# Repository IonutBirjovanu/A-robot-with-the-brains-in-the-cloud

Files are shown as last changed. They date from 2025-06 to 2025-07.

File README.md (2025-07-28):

# Cloud-Controlled Quadruped Robot with GPT Assistant

This project showcases the design and implementation of a 3D-printed quadruped robot powered by a cloud-based Large Language Model (LLM) to enable natural human-robot interaction. Combining embedded electronics, speech recognition, and AI decision-making, the system allows users to interact with the robot using voice commands and receive verbal and physical responses in real time.

---

## Overview

The robot is built around a modular architecture:

- **Raspberry Pi 5** handles high-level control and communication.
- **Arduino Pro Micro** controls the 12 servomotors via a PCA9685 board.
- **Sensors**:
  - Front-facing Pi Camera
  - Two ultrasonic distance sensors
  - Wireless USB microphone
- **Speaker** for voice replies (TTS using `espeak`)
- **Cloud AI Pipeline**:
  - Audio transcription: OpenAI Whisper API
  - Reasoning and dialogue: OpenAI GPT Assistants API
  - JSON response containing movement instructions and speech output

---

## Project Goals

- Combine a physical quadruped robot with a cloud-hosted LLM brain
- Enable speech-based interaction using voice commands
- Integrate real-time multimodal sensing and action
- Demonstrate interactive behavior through high-level LLM planning and low-level hardware execution

---

## Software Architecture

```mermaid
graph TD;
  A[User Voice Command] --> B[Pi Microphone];
  B --> C[Whisper API Transcription];
  C --> D[Prompt + Sensor Data];
  D --> E[GPT-4 Assistants API];
  E --> F[JSON Response];
  F --> G[TTS Output to Speaker];
  F --> H[Serial Command to Arduino];
  H --> I[Servo Movement Execution];
```

---

## Hardware Architecture

The robot is a 12-DOF quadruped platform built on a 3D-printed skeleton, using hobby-grade servos and embedded electronics, organized around a modular control architecture. The system separates high-level logic (handled by a Raspberry Pi) from low-level actuation (handled by an Arduino Pro Micro).

### Mechanical Design

- Based on the **SpotMicro** open-source design
- 3D-printed frame modified to fit:
  - Raspberry Pi 5
  - Battery pack
  - Custom speaker mount
  - Camera and ultrasonic sensors

Each leg has:
- **3 servos**: hip (horizontal), shoulder (vertical), elbow (vertical)
- **Total**: 12 servos, driven by a PCA9685 PWM driver

### Electronic Components

| Component | Role |
|---|---|
| Raspberry Pi 5 | Main computer (AI, sensors) |
| Arduino Pro Micro | Low-level servo control |
| PCA9685 Board | 16-channel PWM servo driver |
| TD-8125MG Servos (×12) | Joint actuation |
| HC-SR04 Sensors (×2) | Distance measurement |
| Pi Camera | Visual input |
| USB Microphone | Voice command capture |
| Custom Speaker | Audio output via `espeak` |
| Buck Converters | Power regulation for Pi & servos |
| 4S 18650 LiPo Battery  | Main power supply |

---

### Modular Hardware Design
```mermaid
graph TD;
    %% Power distribution
    A[4S 18650 LiPo Battery] -->|Power| B1[DC-DC Buck Converter<br>5V for Pi]
    A -->|Power| B2[DC-DC Buck Converter<br>6V for Servos]

    %% Power outputs
    B1 -->|5V Output| C[Raspberry Pi 5]
    B2 -->|6V Output| F[12x TD-8125MG Servos]

    %% Pi peripherals
    C -->|USB| D[USB Microphone]
    C -->|GPIO| H[2x HC-SR04 Distance Sensors]
    C -->|CSI| I[Pi Camera Module]
    C -->|USB| J[USB Audio DAC → Speaker]
    C -->|USB Serial| G[Arduino Pro Micro]

    %% Control path
    G -->|I2C| E[PCA9685 Servo Driver]
    E -->|PWM| F

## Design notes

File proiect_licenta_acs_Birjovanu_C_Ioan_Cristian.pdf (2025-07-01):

## UNIVERSITY POLITEHNICA OF BUCHAREST FACULTY OF AUTOMATIC CONTROL AND COMPUTERS COMPUTER SCIENCE AND ENGINEERING DEPARTMENT

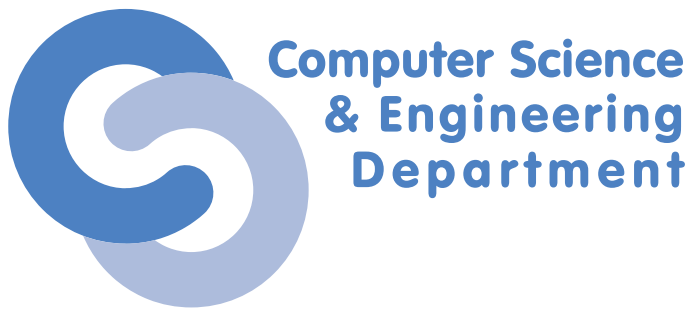
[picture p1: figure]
Computer Science & Engineering Department

# DIPLOMA PROJECT

## A Robot with the Brains in the Cloud Giving a LLM a quadruped robot body

# Bˆırjovanu Ioan-Cristian

### Thesis advisor:

### Conf. Iuliu Vasilescu

### BUCHAREST

2025

### CONTENTS

1 Introduction | 1
2 Background and Related Work | 5
3 Cloud-Integrated Control Software | 10
4 Quadruped Robot Design and Control (Hardware) | 28

5 Experimental results and Discussion | 38
6 Conclusions | 47
Appendix A System prompt | 51
Appendix B Sample Conversation with the Robot | 54

### ABSTRACT

This paper showcases the design and implementation of a quadruped robotic platform controlled by a Large Language Model (LLM) hosted in the cloud. The system aims to achieve a natural interaction between human and robot by offloading the high-level reasoning and decision-making tasks to a LLM, while the robot’s onboard components handles low-level movement control. The project’s architecture integrates a Raspberry Pi as the central piece, interfacing with an Arduino-based motion controller and sensors, including a camera, distance sensors, and a microphone.

A Python script collects the sensor data, including visual input and voice commands, and forwards it to the GPT Assistants API. The assistant processes this data and returns a response that includes movement instructions and a reply, enabling the robot to respond both verbally and physically in real time. The quadruped is based on a 3D-printed structure inspired by the Boston Dynamics Spot Robot, using 12 servomotors controlled via a PCA9685 module and an Arduino Pro Micro.

The paper highlights the two key components: a cloud-integrated AI control pipeline, and the robotic system’s design. Results show that the robot is able to understand spoken commands, respond accordingly, and demonstrate interactive behavior. This prototype provides a foundation for exploring LLM-powered physical agents and opens up possibilities for more advanced human-robot interactions in the future.

### 1 INTRODUCTION

Recent advances in Artificial Intelligence and hardware computing power are allowing robots to achieve higher reasoning and more advanced behaviors by using powerful models. For example, Boston Dynamics’ Spot robot [1] demonstrated the potential of autonomous quadruped robots in real-world scenarios.

Sadly, replicating those capabilities on a hobby-grade project is difficult due to the limited on-board computing capacity and complex software requirements. So, a popular workaround for lower computing capabilities and complexity is to offload the processing to the cloud, by using large language models (LLM’s) to handle high-level perception, reasoning, and decision-making.

This project aims to enhance a relatively low-cost 3D-Printed quadruped robot with a cloud-based intelligence, effectively giving the robot a ”brain in the cloud” that can understand spoken commands, speak with users and plan actions. By integrating a modern LLM (OpenAI’s GPT 4.1 [2]) as the robot’s reasoning system and using a simple onboard microcontroller for motor control, complex interactive behavior can achieved on lower-end hardware. The increased popularity of cloud AI combined physical robotics has the potential to greatly expand the accessibility to intelligent robots in research and education.

### 1.1 Motivation

This project started from an idea I got while watching a video on the OpenAI API [3] and how it could be used to control and navigate a robot around its environment [4]. The idea of creating a robot that would have the awareness of the average AI assistant was very intriguing at the time. After deciding upon using the OpenAI Assistants API for the so-called ”brains” part of this project, I started to look for ideas for the physical frame, the actual robot body. I was not sure what type of robot I wanted for this project, but I always thought about building a quadruped robot, similar to the Boston Dynamics’ Spot [1], and after searching for a ”3D-Printed robot dog”, I stumbled upon the SpotMicro project [5].

### 1.2 Aim and Objectives

The primary aim of this project is to design and implement a quadruped robotic system that combines a physical robot body with a cloud AI based on a Large Language Model(LLM). The robot should be capable of understanding natural language voice commands, responding verbally and with movement actions. To achieve this goal, I had to complete the following objectives:

- Developing a cloud-integrated software stack that can collect multimodal data (audio, video, distance), perform speech-to-text transcriptions, communicate with a GPT-based assistant in the cloud, and interpret the assistant’s replies, including movement instructions.
- Designing a prompt for the GPT assistant so that it produces useful and relevant

responses in a structured JSON format, that can be interpreted by the robot control system.
- Building a quadruped robotic platform inspired by Boston Dynamics’ Spot, using 3D Printing, servo motors for movement (3 per leg) and a microcontroller for the servo control.
- Implementing motion control firmware on the microcontroller that can parse the

high-level movement commands from the assistant and, move the leg servos accordingly (walking, turning, gestures).
- Integrating the sensors (camera, ultrasonic distance sensors, microphone) on the robot

and adding their data in the assistant’s message, enabling basic environmental awareness.
- Evaluating the system in example human-robot interaction scenarios, focusing on

the robot’s ability to execute voice commands, engage in simple dialogue, and move accordingly.

### 1.3 Contribution

This project brings several contributions related to the combined field of AI and robotics. Firstly, it demonstrates a practical architecture for a cloud-enhanced robot, where a local system uses a remote LLM for advanced natural language processing and decision-making. Unlike traditional robots, with all their processing taking place on-board, my project exemplifies the concept of cloud robotics [6], offloading computationally intensive AI tasks to remote servers.

Secondly, it contributes with a software pipeline written in Python[7] that combines Whisper speech-to-text transcription and GPT-4-based dialogue with control logic, illustrating how to integrate these advanced AI services into embedded systems.

Thirdly, this project showcases a custom hardware design for a 12-DOF quadruped robot (mechanically and electronically) and an Arduino control firmware that serves as a helpful robot agent that outputs natural language combined with action commands.

Finally, this work provides an analysis of the challenges (network delay, real-time control difficulties, sensor noise, and servo calibration) that I encountered while working on this project, along with documented solutions and recommended future improvements.

### 1.4 Results

The outcome of this project is a functional prototype of an interactive quadruped robot assistant. The robot can understand spoken user commands thanks to Whisper’s advanced speech recognition[8]. It can engage in a simple conversation with the user using GPT-4, which provides reliable responses to a wide range of questions. The GPT assistant is prompted to output a structured JSON in its replies, that include movement movement commands. Those commands are parsed and sent to the microcontroller, which in turn executes the corresponding servo movements. The robot can perform a set of movements, such as: walking forward, backward, turning left or right, standing, sitting, laying flat, waving and holding paw. Basic obstacle avoidance is demonstrated: if an object is detected by the distance sensors or observed in the camera view, the assistant will choose to not walk right into it, but to either avoid it using a turn command, or ask for a different instruction.

A sample interaction shows the robot engaging in a short dialogue, following a series of movement instructions given by the user, and responding accordingly when an invalid instruction was given (trying to avoid an obstacle that got too close). These results, detailed in the 5th chapter, validate the usefulness of integrating a cloud-based AI controller with a physical robot body. The system’s limitations were also observed - notably the approximately 5 second delay between speaking a command and the robot’s reply and action, due to network speed and API processing times.

### 1.5 Structure

The rest of this paper is organized as follows:

- Chapter 2 gives background information on cloud robotics, large language models, the

Whisper speech recognition model, and existing quadruped robot frameworks that inspired my design.
- Chapter 3 describes the implemented software architecture, including the sensor in-

terfaces, the voice transcription process, the integration with OpenAI’s GPT assistant (prompt design and JSON output parsing), and the logic for sending commands to the microcontroller.
- Chapter 4 details the robot’s hardware design and control: the mechanical construction of the quadruped (CAD and 3D printing), the servo control scheme using a PCA9685 driver, the electronics and wiring, and the Arduino program that interprets commands and generates coordinated leg movements. The physical challenges posed by the servo calibration and the gait stabilization are also mentioned.
- Chapter 5 presents experimental results and a discussion on the system’s performance.

We walk through an example user-robot conversation and analyze the response times, accuracy of the transcription and GPT responses, and the reliability of movement execution. It highlights the current limitations and the trade-offs made in this design (for example, the dependence on a reliable internet connection). In the last section, the future work directions are presented, such as improving autonomy with on-board processing, and expanding the robot’s list of skills.
- Chapter 6 brings and end to the paper, summarizing the achievements made with this

project.

The paper also includes Appendices with additional details: the full prompt given to the GPT assistant defining the robot’s control scheme and command format (Appendix A), and a sample conversation illustrating the robot’s behavior (Appendix B).

### 2 BACKGROUND AND RELATED WORK

### 2.1 Cloud Robotics and AI Assistants

The concept of cloud robotics refers to a robotics architecture where a big part of the computation and data storage are offloaded to cloud infrastructure, enabling robots to benefit from powerful remote resources via network connection. This contrasts with traditional robots that rely only on on-board processing. By using the cloud, even smaller robots can have access to advanced processing – for example, advanced AI models or shared knowledge bases – that would be impossible to run locally on limited hardware. Early versions of cloud robotics included networked robots sharing maps and skills (e.g. RoboEarth project[9]) and offloading heavy tasks like image processing to data centers.

In recent years, the expansion of IoT[10] and faster wireless communication has made cloud-connected robots more practical, and the model is seen in commercial products like Amazon’s Alexa devices[11] and Google’s Home assistants[12] (essentially stationary robots with voice interfaces that rely on cloud AI). This project builds on this idea: the quadruped robot uses the cloud for its AI assistant and voice transcription, which is a form of AI-as-a-Service[13] for robotics. One main advantage for this approach is that improvements or upgrades to the AI (e.g. a newer language model) can be used via an API call without changing the robot’s hardware. The trade-off is that the robot becomes dependent on network connection and suffers from higher latency in control loops, which must be addressed in the system design.

In particular, AI assistants[14] powered by Large Language Models have become accessible via APIs (e.g. OpenAI’s GPT-based services, including the new Assistants API[15]) that allow integration of conversational AI into applications. These assistants can follow complex instructions, retrieve information, and perform reasoning. By defining a suitable system prompt (role and instructions), we can customize the assistant’s reply in specific scenarios. In this project, I created a robotic cloud assistant – a custom GPT-4-based agent designed to interpret sensor data and user requests, then output both a conversational response and a robotic action. This approach is inspired by emerging frameworks like the OpenAI Function Calling capabilities[16], where the model can return structured data (like function arguments or a JSON) in addition to text. Rather than hard-coding robot behavior, we “prompt” the AI with the robot’s capabilities and let it decide the appropriate action, which is an example of using an LLM for high-level robot control. Prior works have started exploring LLMs in robotics: for example, Google’s SayCan[17] and related research combine LLMs with robot perception to plan actions from instructions, and community projects like MachinaScript[18] have demonstrated controlling Arduino-based robots via GPT-generated JSON instructions.

MachinaScript, in particular, outlines a pipeline where a central “brain” (a computer or a Pi) listens for input (voice or visual), uses an LLM to generate a sequence of actions in a structured format, parses these instructions, and then sends them to microcontroller “body” which executes them. My system uses a very similar pipeline, confirming that cloud-based brains for robots are a popular research direction.

### 2.2 Large language Models and GPT-4

Large Language Models like GPT-3.5 and GPT-4 are neural networks trained on massive text databases, capable of generating human-like text and performing a range of language tasks. GPT-4, introduced by OpenAI in 2023, is particularly notable for its ability to handle nuanced instructions and even accept image inputs. It exhibits what OpenAI describes as “human-level performance on various professional and academic benchmarks”, and is more reliable and creative compared to its predecessor. For the purpose of controlling a robot via natural language, GPT-4’s abilities fit well: it can understand context, reason about user requests, and produce intelligent multi-part answers. More importantly, GPT-4 can be guided via prompt engineering[19] to output structured data. We utilize this by instructing GPT-4 to format its responses in JSON with specific fields (like ”speech” and ”action”), effectively turning the free-form text generation into a fixed command interface for the robot.

One challenge with using GPT-4 (or any LLM for that matter) in robotics is ensuring correctness and safety of its outputs. LLMs are stochastic and can produce irrelevant or incorrect responses if not guided properly. They also have no built-in knowledge of a robot’s physical constraints. We fix this by carefully configuring the system prompt given to the model with explicit instructions and examples, explaining exactly which movement commands are available and what they mean. This aligns with how the author of the OpenCat framework[20] integrated ChatGPT with the Petoi Bittle robot dog[21]: by “training ChatGPT to understand what commands Bittle supports”, he made sure that the AI would respond within the robot’s abilities. The result, as reported, was a robot that could communicate and follow instructions with personality, dancing and performing tricks on command.

Similarly, this project’s GPT-4 assistant is made aware of the set of actions that the quadruped can do, and it’s instructed to avoid any output that doesn’t match the JSON format or tries something unsafe (like walking forward into an obstacle). GPT-4’s wide training data also means it can handle general conversations – if the user asks a question unrelated to movement (e.g. a trivia question), the model can answer factually while still remaining “in character” as a robotic dog.

### 2.3 Voice Recognition with Whisper

For the robot to receive commands in natural spoken language, a reliable Speech-To-Text (STT) engine is required. I selected OpenAI’s Whisper model for this task, thanks to its high accuracy and tolerance to noise and accents. Whisper is an open-source neural net trained on 680,000 hours of multilingual data, and it approaches human-level speech recognition performance. Unlike traditional keyword-based voice control, Whisper can transcribe free-form user speech, which is essential since the GPT assistant expects full sentence inputs (e.g. “Can you walk forward a few steps?” rather than a single pre-set command phrase like ”Ok Robot, move forward.”). There are two ways of using Whisper in this project: running it locally on the Raspberry Pi 5, or using a cloud API. Running the small Whisper models on a Pi 5 is doable, but it is quite slow (15-20 seconds for a 10-second long audio recording in my case), and uses a significant portion of the CPU, as noted in recent benchmarks of Whisper software on Pi hardware[22].

I instead opted for the OpenAI’s Whisper API for faster transcription, given that the robot is already internet-connected for the GPT assistant. The recorded audio from the robot’s microphone is sent to the Whisper API, and a text transcription is returned, usually in under 2-3 seconds for a short command. This cloud STT approach uses the cloud robotics philosophy and offloads the heavy lifting from the Pi. However, an offline fallback could be implemented in future versions for limited-case scenarios, making sure that the robot can still respond to basic commands in the absence of an internet connection (at the cost of slower and less accurate transcriptions). It’s worth noting that voice interface technology has a rich background in robotics and consumer devices. Systems like Amazon’s Alexa and Google’s Home Assistant introduced the scenario in which one can speak to a device and get intelligent responses. These systems also perform audio capture locally and send it to cloud servers for interpretation, so quite similar to what’s done in this project. The difference is that my robot does not just respond in words, it also acts with physical actions. This integration of voice commands, dialogue, and a physical body is a step towards more natural human-to-robot interaction. It was important to make sure that the transcription is accurate, especially for command phrases like “stop”, “forward”, “turn left”, since any misinterpretation there could lead to a wrong movement. Whisper’s accuracy on those simple words was great in testing, even with a bit of background noise and weird accents, thanks to its advanced speech recognition.

### 2.4 Quadruped Robot Platforms and Spot Micro

The mechanical design of my robot takes inspiration from existing open-source quadruped projects, particularly the Spot Micro family of hobby robots[23]. Spot Micro is a scaled-down, 3D-printed version of Boston Dynamics’ Spot, typically using 12 servos (3 per leg) forming the main joints: hip (horizontal translation), shoulder (vertical rotation), and knee (vertical translation). This provides a total of 12 degrees of freedom, which allows the robot to perform a wide range of leg motions and poses. Many makers have contributed with variants for Spot Micro. For example, the Nova Spot Micro project by Chris Locke[24] provides STL files and assembly guides for this robotic framework.

My robot uses a modified version of these community designs, adjusted to fit my specific components (The Raspberry Pi 5, a camera module, the speaker etc.). Low-cost quadrupeds like Spot Micro use hobby-grade servos for actuation. Common choices are metal-geared servos such as the TowerPro MG996R or DS3218, which provide decent torque (10-15 kgcm) at 6V and are affordable. However, as noted by hobbyists, a fully assembled Spot Micro can weigh a few kilograms, and using cheap or plastic-gear servos isn’t enough, as they will not be able to support the robot’s weight and can fail. In the beginning, I tried using TowerPro MG996R servos in my robot, but they proved to be difficult to work with (more details in Chapter 5). The servo calibration is an important process as well: each servo’s zero position must be aligned correctly when assembling the legs, and some trim adjustments have to be coded in, so that the robot stands evenly. The Nova Spot Micro project prioritizes calibrating the motors during leg assembly for proper movement. In my build, I used a servo tester (https://www.optimusdigital.ro/en/others/1162-tester-pentru-servomotoare.html) to get the correct angles while mounting the servo horns, making sure all the joints are symmetric.

Several electronic control architectures exist for DIY quadrupeds. One approach (used by Petoi’s commercial Bittle and Nybble robots) is to use a microcontroller (like an Arduino (https://www.arduino.cc/) or a Teensy) (https://www.pjrc.com/teensy/) for reading sensors and driving servos, and an optional Raspberry Pi (https://www.raspberrypi.com/) or ESP32 (https://www.espressif.com/en/products/socs/esp32) for higher-level tasks. Another approach is to use a microcontroller purely for motion control and a companion board (Pi or another MCU) for higher level logic and sensor data. My design uses the second approach: the Arduino Pro Micro (https://store.arduino.cc/products/arduino-micro) is used for servo control (“the body”), and the Raspberry Pi acts as the high-level processing unit for the sensor data and movement commands (“the brain”). This separation is useful because the servo pulses handled by the Arduino require precise timing, while the Pi, which runs a full Linux OS and resourceintensive software, can occasionally lag or spike in latency. This split architecture is also seen in OpenCat, (https://www.petoi.com/pages/opencat-open-source-robot-pet-framework) an open-source quadruped framework, which uses an Arduino-compatible board for locomotion and an optional Raspberry Pi for running AI algorithms.

Finally, we’ll look at the gait (https://www.animatornotebook.com/learn/quadrupeds-gaits) and control software in related work. Fully dynamic autonomous quadrupeds (like Boston Dynamics’ Spot) (https://bostondynamics.com/products/spot/) use advanced control algorithms, sensor arrays (IMUs, (https://en.wikipedia.org/wiki/Inertial_measurement_unit) vision, lidar (https://en.wikipedia.org/wiki/Lidar) etc.), and even machine learning to achieve advanced navigation. In the hobby space, simpler gaits (like crawling gaits where at least 3 legs touch the ground) or predefined walking sequences are typically implemented. Some projects use inverse kinematics (IK)[25] to compute leg joint angles for the desired foot positions, providing more flexibility in movements (e.g. the Alpha ESP32 Spot Micro[26] uses IK for motions like sitting and walking.

IK requires solving the servo angles for given desired XYZ positions of the feet relative to the body. I opted for not using IK in the leg positioning because of the issues encountered with the MG996R servos. (https://towerpro.com.tw/product/mg996r/) Instead, my robot’s walking gait is encoded as a series of key frames (servo angle sets) that move the legs in a cycle – an open-loop (https://focuskeeper.co/glossary/what-is-open-loop-system) approach. This method is enough for demonstrating walking on flat ground, though it lacks the adaptability of a full IK or feedback-controlled gait[27]. The implications of this choice (stability vs flexibility) are discussed in Chapter 4 and Chapter 5.

In summary, this project takes inspiration from prior work in cloud-connected AI, voice interfaces, and quadruped robotics. By combining these elements – a cloud AI assistant, a voice-controlled interface, and a quadruped platform, this project makes a solid entry in the interactive personal robotics space.

### 3 CLOUD-INTEGRATED CONTROL SOFTWARE

### 3.1 System Architecture Overview

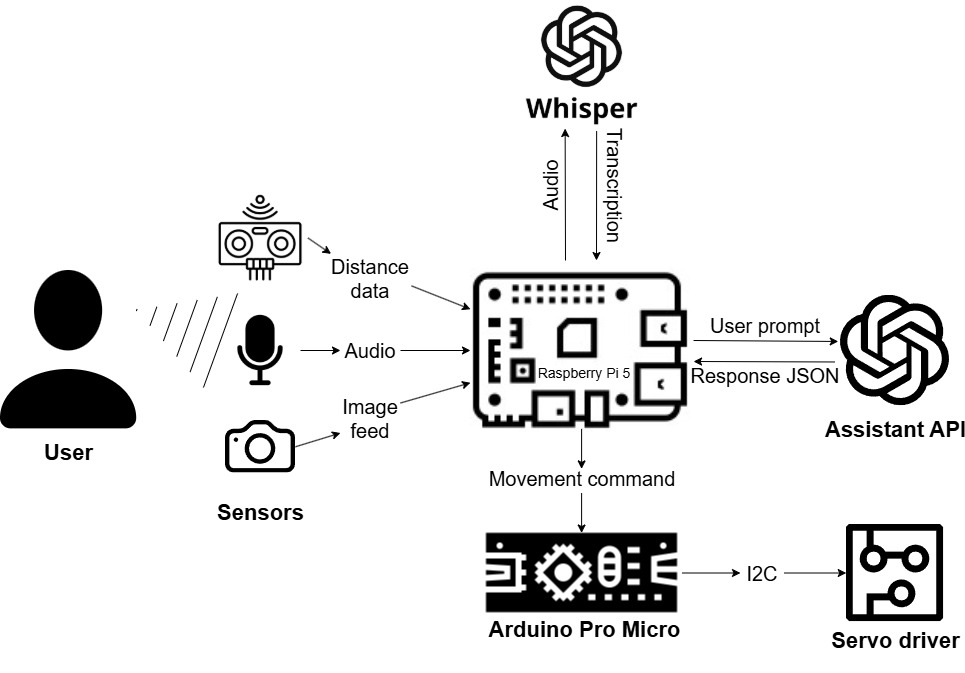
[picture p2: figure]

Figure 1: High-level system architecture, showing the flow from sensor input to robot motion.

The core of my system[28] is a pipeline that connects human input to robot action output via cloud API’s. Figure 3.1 illustrates the architecture. A user’s voice command is captured by the robot’s microphone, along with a picture from the Pi camera (https://www.raspberrypi.com/documentation/accessories/camera.html) and the data from the distance sensors, and then it is processed by the Raspberry Pi 5 (the onboard computer). The Pi runs a Python-based program that executes the following steps:

1. Input Reception: The raw audio is recorded at the beginning of the control loop for 10 seconds, then sent to the cloud-based Whisper API for transcription. The script also captures a picture from the front-facing camera and the distance readout from the 2 distance sensors, also mounted up front.
2. LLM Query Formation: The transcribed text from the user’s recording, along with the sensor readings (distance measurements and the camera feed), is formatted into a prompt, and sent to the GPT-4 assistant API. The assistant has been configured with a system prompt that gives it context about being a robot control system, the input data, its moveset, and the required response format.
3. Assistant Processing in the Cloud: The GPT-4.1 model, running on OpenAI’s servers - the “brains in the cloud” - receives the query and generates a response. Thanks to the given prompt, the response is a JSON object containing two main parts: a natural language reply to the user (the ”speech” field), and a set of movement commands (the ”action” field, which may contain a keyword like ”forward”, ”turn-left”, etc., or a direct control structure with parameters, and the ”steps” field - how many steps of the movement should the robot make).
4. Response Handling: The Raspberry Pi parses the JSON response. The ”speech” reply is extracted and is output via the speaker (running the Espeak text-to-speech (https://espeak.sourceforge.net/) software), and displayed (for debugging purposes, I logged it to the console). The action instructions are translated into a series of movement commands, which are sent over a serial connection to the Arduino board.
5. Microcontroller Servo Control: The Arduino receives the serial commands and executes the corresponding servo movements (e.g. starting a walking sequence or turning). This is the final step of the input-reasoning-action loop. After the Arduino reports back via Serial that the movement is finalized, the Python script will repeat all of the steps from above in the next loop.

With this architecture, the Raspberry Pi works as an intermediary between the cloud AI and the robot’s body. It handles all network communication and local sensor data. The Pi runs a Python script: it firstly configures all the components at the startup (the camera, Arduino Serial and the distance sensors) and announces via the TTS that the robot has successfully initialized, then it runs in a loop format: it asks for a command from the user, starts recording 10 seconds of audio, sends that recording to the Whisper API for transcribing, then, after the transcription is done, it packages it, alongside the camera picture and the distance sensors readout into a prompt, and sends it to the GPT assistant API for processing. I chose Python thanks to its vast library collection (for example, using the OpenAI Python library (https://github.com/openai/openai-python) to access the GPT assistant, and serial library for Arduino (https://pyserial.readthedocs.io/en/latest/pyserial.html) communication) and ease of use. In terms of performance, Python on the Pi 5 runs smoothly overall. Also, because the time constraints aren’t critical since the servo control is offloaded to the Arduino, I haven’t encountered any problems regarding the functionality of the robot. There are some delays introduced by the network, the AI processing times and the audio recording, but they don’t affect the functionality of the robot, and since the STT software is configured to run on a separate thread, the real-life experience doesn’t include significant delays.

The data flow and message formats are very important in this architecture. The recorded audio is handled in chunks of 10 seconds – the program loop starts a 10-second audio recording after a TTS message (in my case it’s ”Please give an instruction”). The audio is saved as a WAV file (https://en.wikipedia.org/wiki/WAV) and sent to the Whisper API. The returned transcription is inserted into the assistant prompt in the ”user instruction” field. Sensor data (the two ultrasonic distance readings in cm) is encoded as a small JSON snippet. For example, we have the ”environment data” field indicating 45 cm to an obstacle in the left and 50 cm to the right. This is due to the sensor angles being 50 degrees towards the center:

environment_data = (
"Left sensor: 45 cm (50° right-inclined), " "Right sensor: 50 cm (50° left-inclined)." )

These values are included in the user prompt to the assistant, alongside an image capture from the front camera. The GPT JSON reply will look like this:

{
"movement": "forward",
"steps": "4",
"speech": "Okay, I will walk forward."
}

Then, the Pi would process the output JSON. It will speak the ”speech” text using the TTS program and send the movement commands to the Arduino for the servo movement. In other interactions, the assistant might return something like this:

{
"movement": "left,forward,right",
"steps": "3,5,3",
"speech": "Obstacle detected. Walking around it."
}

Here, it observed from sensor data and camera feed that the forward path is blocked by an obstacle and decided to go around its left side. More details about the JSON structure in section 3.4.2.

One important addition is that I implemented basic error handling in the Pi’s software. If the Whisper API fails to return a valid transcription (network issue) or returns an empty one, it will fallback to a default case (”There are no instructions, act on your own”). If the GPT API call fails or returns invalid JSON, the Pi will log an error and retry in the next loop. To keep the processes in sync, only one GPT query is active at a time. Once the Arduino finishes executing a movement, it will send a “Finished Instruction” signal over serial, which the Pi listens for. This process helps to synchronize command execution (the Pi won’t send a new movement command until the old one is finished).

Overall, the system architecture represents a modular design: the cloud AI module, the Pi control module, and the microcontroller module work independently and connect through clear interfaces (API calls and serial commands). This modularity allows for future upgrades, such as using a fallback local LLM, adding additional sensors, or upgrading the hardware, all without rethinking the entire system.

### 3.2 Sensor Suite and Data Collection

The robot is equipped with a general set of sensors used for gathering the environmental context and the user instruction:

- Camera: A Raspberry Pi Camera Module (https://www.emag.ro/camera-ir-cut-compatibil-raspberry-pi-b-4b-ai478/pd/DY11J7MBM/?oid=240957149&scenario_ID=1) is mounted in the front of the robot and used

for capturing images of what is in front of the robot. In the current implementation, I didn’t add any on-board image recognition to run on the Pi, since I wanted to ”test” how much context would the AI be able to gather from the picture alone. Future versions could implement an object tracking feature and face recognition, so the robot could recognize users when looking at them and reply based on the person it’s talking to. The camera takes one picture for every loop, so every prompt sent to the assistant API includes visual data for context.
- Distance Sensors: Two HC-SR04 ultrasonic distance sensors (https://www.sparkfun.com/ultrasonic-distance-sensor-hc-sr04.html) are located in the front

of the robot, on one side and the other of the camera, each angled inward by 50 degrees. They are positioned like this purely because of the way the Spotmicro model (https://www.thingiverse.com/thing:3445283) is designed. The Raspberry Pi interfaces with these sensors through its GPIO pins (the trigger and echo pins for each sensor). The time (https://www.programiz.com/python-programming/time) Python library was used to handle the timing (emitting a 10 µs trigger pulse and measuring the echo pulse width for distance). These

values are then added to the prompt every time a query is made. The assistant can use this information to decide on movements. For example, if the right ultrasonic records a small value (less than 15 cm), the assistant will suggest avoiding the obstacle from the left (due to the inwards angle, these sensors help the robot determine the lateral obstacles, that aren’t covered by the camera FOV). Basically, the ultrasonic distance sensors give the robot a basic idea for obstacles, like the simple collision avoidance in a vacuum cleaner robot. (https://www.pcmag.com/picks/the-best-robot-vacuums) While GPT is not performing advanced path planning, it can output sentences like “I sense an obstacle in the right, I will turn left”, which proves a good environment awareness.
- Microphone A USB Wireless Microphone (https://www.alibaba.com/product-detail/Manufacturer-customized-round-2-4Ghz-mobile_1600363962435.html) is connected to the Pi for capturing audio

from the user. Since Whisper is optimized for noisy and unclear audio, the quality of the mic doesn’t have to be great. Although, these wireless mics are quite decent, and the rezulting transcriptions rarely differ from the real spoken phrase. The Python script uses the Arecord (https://linux.die.net/man/1/arecord) Linux library for recording audio. It opens a subprocess with the arecord command, selecting a 16kHz rate and mono audio channel, which is the recommended Whisper audio format. The audio is the only source of input from the user, and is automatically recorded in 10-second batches at the beginning of the script loop. A future improvement could include a separate program thread that continuously records audio, and when it detects voice activity (some noise after a period of silence), it sends that snippet to the Whisper API for transcription, avoiding the 10-second pause in the robot control loop for when the audio is recorded. Some specific voice commands could also be added, like the addition of a ”force-stop”, where the robot would suddenly stop when hearing the word ”stop” or ”pause” from the user.

### 3.3 Voice Command Transcription

The voice command segment converts the user’s speech into text that can be sent to the GPT assistant. As presented earlier, I chose the OpenAI Whisper transcription model (https://openai.com/index/whisper/) for this task. The whole transcription process works like this:

- At the beginning of the loop, after a spoken announcement via the TTS (”Please give an instruction”), the script starts recording a 10-second segment of audio, using the arecord Linux library. The recording segment of code is:

command = [
"arecord",
"-D", AUDIO_DEVICE,
"-f", AUDIO_FORMAT,
"-c", AUDIO_CHANNELS,
"-r", AUDIO_RATE,
"-d", str(RECORD_SECONDS), AUDIO_FILE
]

try:
subprocess.run(command, check=True)
print(f"[Audio] Recording complete. File saved as: {AUDIO_FILE}") except subprocess.CalledProcessError as e:
print(f"[Error] Recording failed: {e}")
- The recorded audio is then sent to either the Whisper API for transcription, or tran-

scribed locally using whisper.cpp. (https://github.com/ggml-org/whisper.cpp) The transcription method is decided by the boolean configuration variable USE API WHISPER (it has the value ”True” if we want to use the API, and ”False” for the local api). The audio transcription is sent to the Whisper API via this code:

transcript = ""
# Use the API to transcribe the audio print("[Whisper] Transcribing audio with API...")

try:
# Open the audio file

audio_file = open(wav_file, "rb")

except FileNotFoundError:
print(f"[Whisper] WAV file not found: {wav_file}")

try:
# Call the API to transcribe the audio

transcript = client.audio.transcriptions.create( model="whisper-1",
file=audio_file
)

except Exception as e:
print(f"[Whisper] Error during transcription: {e}")
- Next, we get the resulting JSON from the call, and extract the ’text’ field containing

the recognized speech. Whisper tends to include punctuation quite well, so I opted to send the direct transcription to the assistant API, to keep a small bit of context that would’ve been lost from text post-processing. One interesting observation though
- Whisper will transcribe everything it hears, so if the user says something and then there’s a prolonged silence or an ”umm...”, it will also include that. In the case where no speech was detected and Whisper returned an empty string, I added a feature so that the command will be changed to ”There are no new instructions, act on your own”.

The latency introduced by the transcription isn’t noticeable: recording 10 seconds of audio adds 10 seconds. Uploading that to the API and waiting for the transcription takes 2-3 seconds, which isn’t a long time. This is similar to a conversation with other popular voice assistants(Gemini, Siri, Alexa, where similar delays exist). Whisper can operate in different modes (translating to English, or just transcribing). I set it to translate to English since there are instances where the robot would be spoken to in my native language (Romanian).

Using Whisper yielded a high accuracy - in testing, even pretty complex phrases were correctly transcribed. Whisper’s tolerance to noise eliminates the need for a noise cancellation step. In one test, background music at an average volume did not affect the understanding of the command ”turn right” – it was transcribed correctly. This performance proves that using a modern AI-based automatic speech recognition (ASR) is a valid method for human input.

### 3.4 GPT Assistant Integration

This section describes the interface with the GPT-4.1 model via OpenAI’s API and how I configured the assistant’s output to match the robot’s architecture. The integration has two main components:

1. The Prompt Design, (https://www.promptingguide.ai/introduction/tips) which is responsible with the construction of messages (system and user prompts) sent to GPT-4 to receive the desired output.
2. The JSON Response Format and parsing, which describes how the Raspberry Pi extracts the assistant’s reply and the movement commands to be sent to the microcontroller.

### 3.4.1 Prompt Design

Designing the system prompt (also known as the initial instruction for the AI) is a very important step. My goal was to make the GPT-4 model act as a robot control system for a quadruped robot dog. The assistant has to include movement commands for every reply. I kept adding details for the system prompt as I developed each feature of the project and through experimentation. The final prompt (full text provided in Appendix A) can be summarized in these steps:

- Establishing identity:

You are a robotics control system for a quadruped robot. You receive:
1) The data from the robot’s distance sensors and an image of what he sees through its camera. The camera and the 2 distance sensors are frontally mounted. The camera is oriented straight ahead, and
the sensors are 5cm apart(on one side and the other of the camera), each rotated inwards by 50 degrees.
2) A user instruction - a voice command transcribed into text.

Give the robot a playful and curious personality, eager to discover the environment and people nearby.

- Establishing desired output format and clarifying the movement set:

You must output a JSON object with the following format:

{
"movement": "STRING", | // The actions that the robot will execute
- must be one of: forward, backward, left, right, stand, flat, sit, paw, greet . The actions are sepparated by commas
"steps": list of numbers, // Number of steps done for each movement,

only the forward,backward,left and right commands require a number of steps, for the others the number can be 0
"speech": "STRING" | // The text the robot should speak via TTS
}

Clarification and brief explanation of the poses:
- forward: the robot steps forward once, for around 4cm
- backward: the robot steps backward once, for around 4cm
- left: the robot spins left for one step, for around 10 degrees of rotation
- right: the robot spins right for one step, for around 10 degrees of rotation
- stand: the default position of the robot, standing straight
- flat: the robot lies down, touching the ground with its belly, similar to

its powered-down state
- sit: the robot sits like a dog, good for an idle position
- paw: the robot stretches one of its front feet in the front
- greet: the robot waves with an arm

This tells the model how to reply, making sure that the output can be parsed by the Pi.
- Valid output JSON examples:

Example of a valid json:
{
"movement": "forward,left,sit",
"steps": "2,5,0",
"speech": "Hello, I am moving forward, turning left, then sitting down" }

You can also only send one movement, like this:
{
"movement": "forward",
"steps": "5",
"speech": "Hello,I want to explore, moving forward" }

I listed some examples of valid output for the model.
- Guidelines:

Guidelines:
- Always return a valid JSON.
- If the space permits it but the instruction is unclear, try to turn the robot to the user and ask for clarification.
- If the users request is unclear, and the space is constrained so that you can’t turn, set the movement to a stationary position, steps = 0, and in speech, clarify what you need.
- As long as the space permits it, try and explore the environment you’re in, unless given a clear command from the user.
- Steps values should be integers.

These guidelines were added to increase the answer reliability and set the desired action responses.

I also added an experimental direct control schema to the prompt: instead of a default movement like ”forward”, or ”left”, the agent could send the angle position for every servo index. This was mostly implemented to test the reasoning capability of the GPT model for the direct positions. The prompt is:

There is also the option of a direct position control: You could have a json like this:
{
"movement": "1:30 2:80 5:100,2:60",
"steps": "2,0.5",
"speech": "Hello, I am moving the servos directly now"
}

In this way, you can directly set the angles for each servo on the robot. The movement consists of a list of servo indexes and their values. Different positions are sepparated by commas. The steps value now represents the amount of time each direct position is held.
The positions don’t reset after the timeout, the legs remain in those positions, but you can use the delays for orchestrating new movements. You can set a position, put a step value that determines the time it holds that, then add a new movement with a new time period to create your own complex movements.

The indexes of the servos are:
Each leg: [hip, shoulder, elbow]
{0, 1, 2}, | // Front left
{4, 5, 6}, | // Front Right
{8, 9, 10}, | // Rear Left
{12, 13, 14} // Rear Right

The indexes go from 0-15, but we’re not using the 3, 7, 11 and 15 indexes.

The positions for each servo that the robot uses in the standing pose are:
{40, 50, 65}, | // FL
{100, 90, 80}, | // FR
{45, 100, 80}, | // RL
{90, 60, 70} | // RR

And the positions for the laying flat pose are:
{0, 15, 65}, | // FL
{140, 130, 80}, | // FR
{0, 140, 80}, | // RL
{140, 10, 70} | // RR

The angles go from 0-180, but I recommend only going up to ~140-150, and be careful with the elbow 2, 6, 10, 14 servos - they have less movement space because of the robot’s joints, and can try to bend into the frame, so not reccomended to flex them a lot.

More info about the direct control schema can be found in Section 3.5.

All these instructions were combined into a single system message. This resulted in a long prompt (several hundred tokens), but GPT-4 does not have any problem with that context length. I configured it as the system prompt in the OpenAI’s Assistants Playground. (http://medium.com/@niall.mcnulty/how-to-create-an-assistant-in-the-openai-playground-a-beginners-guide-4f5c5c12213a) then the user message (which contains the transcribed command and sensor data as described).

While testing the assistant, GPT-4 performed great with this prompt. I didn’t encounter any scenarios where the LLM output didn’t match the desired JSON format, and the environmental awareness was almost surprinsing. Again, more details about the results can be seen in the fifth Chapter.

### 3.4.2 JSON Response Format

The formatting of the AI’s response is very important, since the script running on the Raspberry Pi needs to read the movement instructions automatically. I chose the JSON format because it’s easy to parse in Python (using the Python json library (https://docs.python.org/3/library/json.html) ). The content of the JSON is basic: a ”movement” string, a ”steps” list and a ”speech” string.

To ensure that the LLM always returns a JSON, I set the ”Response format” field as a ”json object” in the assistants Model configuration. Also, the design of the JSON output means the system can easily be extended or integrated with other modules. For example, if we wanted a GUI to display what the robot wants to do, it can parse the same JSON. Or, if the Arduino got replaced with another microcontroller, the integration remains the same if it receives the same action strings.

### 3.5 Movement Commands

After the Raspberry Pi extracts a movement command (”movement” string) from the assistant’s response, it will send it to the Arduino, which controls the servos. The communication between the Pi and Arduino is achieved via a USB serial connection (the Arduino Pro Micro appears as a /dev/ttyACM0 serial device for the Pi). I configured the serial link at 115200 baud. The command protocol used designed for serial communication is simple: Each command is sent as a line of text, terminated by a newline character (”\n”). The Arduino program reads lines from serial and parses them. There are 2 types of commands:

1. Movement Commands: Sending a direct moveset command, like ”forward” or ”sit”.

The Arduino moves the servos in predefined positions based on the selected movement. In case of walking commands (e.g. ”forward”, ”backward”, ”left”, ”right”), the ”steps” field represents the number of times that moveset is executed (e.g. for ”left,2”, the robot takes 2 steps to the left). For the rest of the moves that represent just a pose (e.g. ”stand”, ”sit”, ”greet” etc.) the prompt instructs the AI to send a ”steps”=”0” value.
2. Position Commands: Sending a string with direct servo target angles by order index, like ”0:15 1:30 2:90”. This type of command was mostly used for debugging, but with enough details in the prompt, the LLM was able to control the servos directly as well. But, since the aim was to let the AI handle high-level planning, and have the low-level control run on the Arduino, the first option is used by default, leaving the second one for isolated cases.

To send the commands, the serial port has to be initialised first, so I open the serial with 115200 baud rate at the beginning of the script, and keep it open, to avoid resetting the Arduino mid-run. I also set timeout=1 so that reading from serial doesn’t block the script for too long. The Arduino will send back completion messages, like ”Finished instruction” or debugging info like ”Standing still”. Those are printed by the Python script for logging. On the Arduino side, the serial parsing is done in a simple loop: it reads words from the lines until the newspace, then compares the keyword from the received command against known commands. The code looks like this:

void loop() {
// Accept commands via Serial Monitor for now if (Serial.available()) {
String line = Serial.readStringUntil(’\n’); line.trim();
if (line.length() == 0) return;

if (line.startsWith("move,")) {
int first = line.indexOf(’,’);
int second = line.indexOf(’,’, first + 1);
String dir | = line.substring(first + 1, second);
int steps | = line.substring(second + 1).toInt();

if (dir == "forward") moveForward(steps);
else if (dir == "backward") moveBackward(steps); else if (dir == "left") moveLeft(steps);
else if (dir == "right") moveRight(steps); else if (dir == "stand") standPosition();
else if (dir == "flat") layFlatPosition(); else if (dir == "sit") sitPosition();

else if (dir == "paw") pawPosition(); else if (dir == "greet") salutePosition(); else standPosition();

Serial.println("Finished instruction.");
}

An important part of sending the movement commands was avoiding their overlap. I had to make sure that the Pi doesn’t send commands faster than the Arduino can execute them. So, if the robot receives multiple commands from one LLM query, it will send them in order, and wait for the Arduino to reply via serial with the ”Finished instruction.” string, so that it knows to hold on to the new command until the current completes. To achieve this, I implemented a busy-waiting (https://en.wikipedia.org/wiki/Busy_waiting) sequence of code that continuously reads the serial output until it detects the finished instruction string. While testing, because interactions are sequential and the received commands have relatively low numbers (1-3), this configuration worked well. The program loop waits until the robot finishes moving (which is only a second or two per position command, but around 5 seconds for a step forward/backward or a directional left/right). After the movement finishes, it restarts the loop with the recording of instructions and sensor data collection.

In summary, the movement command mechanism is a lightweight protocol that sends the “movement action” from the Pi to the Arduino. In the case of movement commands (which are mostly used unless special cases), it is doing a level of abstraction for the details of the servo movements and gaits, so the high-level AI doesn’t have to calculate the kinematics for the movement. This kind of separation is recommended in robotics: the high-level planner (AI) gives abstract actions and the low-level controller takes care of the precise movement. This approach is also seen in MachinaScript (https://github.com/babycommando/machinascript-for-robots) for example, where they use serial commands like ”A:45,10;B:0,10;” to specify servo targets, so very similar to my direct position approach. Though, my movement command is even higher-level (just choosing a pre-set command). Both methods have their pros and cons.

### 3.6 Movement Gaits

After I finished assembling the legs, I discovered a step that I overlooked: I didn’t know how to make the robot walk. I could have started from a community Spot Micro project and use its locomotion code, but I chose to implement it myself, which in retrospect wasn’t a great idea. So, I first started out by configuring the servos to have the robot stand up straight, using these values:

// The offsets for each leg servo
uint8_t legOffsets[4][3] = { {40, 50, 65}, // FL

{100, 90, 80}, | // FR
{45, 100, 80}, | // RL
{90, 60, 70} | // RR
};

Then, I implemented a function that changed the leg angles relative to the standing position, so it would be easier to code movements for it:

// Set servo angles relative to per-leg offsets
void setLegRelativeAngles(uint8_t legIndex, int8_t hipDelta, int8_t shDelta, int8_t elDelta) {
setLegAngles(

legIndex,
constrain(legOffsets[legIndex][0] + hipDelta, 0, 180), constrain(legOffsets[legIndex][1] + shDelta, 0, 180), constrain(legOffsets[legIndex][2] + elDelta, 0, 180) );
}

And after experimenting with this relative angle change function, I ended up with this forward gait:

void stepForwardCycle() {
// Phase 1: Lift FL + RR
setLegRelativeAngles(0, -10, -10, -10); setLegRelativeAngles(3, 10, -10, -10); delay(100);

// Phase 2: Swing FL + RR forward setLegRelativeAngles(0, -10, 20, 0); setLegRelativeAngles(3, 10, 20, 0); delay(100);

// Phase 3: Place FL + RR down setLegRelativeAngles(0, 10, 20, 0); setLegRelativeAngles(3, -10, 20, 0); delay(100);

// Phase 4: Lift FR + RL
setLegRelativeAngles(1, 10, 10, 10); setLegRelativeAngles(2, -10, 10, 10); delay(100);

// Phase 5: Drag FL + RR backward setLegRelativeAngles(0, 0, 0, 0); setLegRelativeAngles(3, 0, 0, 0); delay(100);

// Phase 6: Swing FR + RL forward setLegRelativeAngles(1, 10, -20, 0); setLegRelativeAngles(2, -10, -20, 0); delay(100);

// Phase 7: Place FR + RL down setLegRelativeAngles(1, -10, -20, 0); setLegRelativeAngles(2, 10, -20, 0); delay(100);

// Phase 8: Lift FL + RR
setLegRelativeAngles(0, -10, -10, -10); setLegRelativeAngles(3, 10, -10, -10); delay(100);

// Phase 9: Drag FR + RL backward setLegRelativeAngles(1, 0, 0, 0); setLegRelativeAngles(2, 0, 0, 0); delay(100);

standPosition();
}

I implemented the simplest mode of stepping forward on a quadruped, by lifting 2 legs at once, in the opposite sides of the robot (the front left leg with the back right leg, ant the front right with the back left), moving them forward, placing them down and dragging them back.

For the backwards stepping, I implemented those same steps, but mirrored the angles so the legs move backwards.

The turning gaits proved more challenging to program, but I ended up using the same strategy, lifting 2 legs at once and moving the other 2 to achieve the desired motion:

void turnLeftCycle() {
// Phase 1: Lift FL + RR
setLegRelativeAngles(0, -10, -10, -10); // FL setLegRelativeAngles(3, 10, -10, -10); // RR delay(100);

// Phase 2: Swing FL back + RR forward
setLegRelativeAngles(0, -10, 20, 0); | // FL backward
setLegRelativeAngles(3, 10, -20, 0); | // RR forward
delay(100);

// Phase 3: Place FL + RR down
setLegRelativeAngles(0, 10, 20, 0); | // FL
setLegRelativeAngles(3, -10, -20, 0); | // RR
delay(100);

// Phase 4: Lift FR + RL
setLegRelativeAngles(1, 10, 10, 10); | // FR
setLegRelativeAngles(2, -10, 10, 10); | // RL
delay(100);

// Phase 5: Reset FL + RR to neutral (drag forward/backward) setLegRelativeAngles(0, 0, 0, 0); // FL setLegRelativeAngles(3, 0, 0, 0); // RR
delay(100);

// Phase 6: Swing FR back + RL forward
setLegRelativeAngles(1, 10, 20, 0); | // FR backward
setLegRelativeAngles(2, -10, -20, 0); | // RL forward
delay(100);

// Phase 7: Place FR + RL down
setLegRelativeAngles(1, -10, 20, 0); | // FR
setLegRelativeAngles(2, 10, -20, 0); | // RL
delay(100);

// Phase 8: Lift FL + RR again setLegRelativeAngles(0, -10, -10, -10); // FL setLegRelativeAngles(3, 10, -10, -10); // RR delay(100);

// Phase 9: Reset FR + RL to neutral setLegRelativeAngles(1, 0, 0, 0); // FR setLegRelativeAngles(2, 0, 0, 0); // RL delay(100);

standPosition();
}

Although complete, the movement code could greatly benefit from further development and testing to optimize and improve it. There is also the option of implementing inverse kinematics (https://en.wikipedia.org/wiki/Inverse_kinematics) to improve movement.

### 3.7 Software Challenges and Trade-offs

Designing the software pipeline raised a couple of challenges, and I had to make some trade-offs. They are listed below:

- Latency and Real-Time Interaction: As mentioned, the total time from speaking a

command to an action execution took a few seconds. This is mostly due to the cloud API calls (Whisper and GPT-4) and the set 10-second recording time, instead of an automatic speech detection. While GPT-4 is very advanced, its replies take a bit of time: typical API response time for a short prompt and short answer was 3-4 seconds in my tests (which is quite good for a modern LLM). Adding the 2-3 seconds for Whisper and some overhead, I often got 5-6 seconds of latency in total. This latency, while noticeable, since it’s not exactly instantaneous, it’s decent in a conversation context. The user experience is also helped by the filler phrases I added via the TTS (e.g. the phrase ”Processing instruction..”, which runs on a separate thread, so it doesn’t have to wait for the api calls). There is also the option of using a faster model, like the GPTo4-mini, which could respond faster (1-2 seconds), but in practice the bigger model also performed well.
- API Reliability: Relying on external APIs adds extra points of failure. There were instances of network issues where the API calls would return error messages (due to failing to connect to the servers). But since the program runs in a loop, it uses a simple retry logic: if Whisper API call fails, the current loop will have no new instruction, and the GPT will act on his own. And if the GPT call fails, there will be no new actions, and the loop will start again. Thankfully, in my use case, the frequency of commands is quite low, so I never got close to the official rate limits of OpenAI (which allow much more requests per minute for Whisper and chat). Another important trade-off is the token cost: (https://openai.com/api/pricing/) each Whisper and GPT-4 API call costs money (although a very small amount per call). Over heavy use it can add up, which is not ideal for a freely roaming robot. For this prototype project though, it was fine (I barely ended up using 60 cents, and the minimum payment of credit for api calls is 5 dollars - so it’s not a real issue for a hobby project). But in the case of a commercial product or widespread deployment, the api pricing becomes meaningful - so a fully offline solution would be preferable in that case. The local processing is also something to consider for future work.

- Continuous Listening vs Set Interval of Recording: I initially wanted the robot

to be continuously listening for a wake word, like “Hey Robot!”. Implementing a wake word detector (like the Porcupine (https://picovoice.ai/docs/quick-start/porcupine-python/) or pyttsx3 (https://pypi.org/project/pyttsx3/) libraries) on Pi is doable, but integrating that with Whisper proved more difficult (so that I didn’t end up constantly sending audio to Whisper, which would consume more resources). In the end, I went with a 10-second listening period announced via TTS at the beginning of the loop, so that the structure would remain more back-and-forward between the user and the robot (the robot listens for a command, processes it, executes it and starts again). The trade-off is between technical complexity and user experience. But for a more advanced process, there would be a need to integrate a local wake-word model to trigger the rest of the pipeline only when the user addresses the robot, and let it act independently in the meantime.
- Sensor Data in the GPT Prompt: Sending sensor data to GPT helped with obstacle

avoidance. But GPT-4 is not a dedicated path planning algorithm, so it might not always know what to do with the sensor values. For example, if there is an obstacle in the front of the robot, and the user says ”go forward”, ideally GPT should output a refusal or walkaround action. The prompt tells it to do so. In tests, it did respond as expected most of the times, but sometimes it might say: ”I’ll try to move forward carefully.” which is not ideal because it’s ignoring the obstacle in a way. This highlights that using a general AI for critical logic requires very explicit instructions. A fix to this problem could be to add a rule in the code (e.g. the Pi checks the distance and changes any forward command with a stationary one, adding a mention to the command change in the next prompt to the assistant). I didn’t end up implementing a safeguard, since the GPT prompt itself was enough, but it is a good implementation idea for future work.
- Memory and Context: I used the assistants API for the GPT calls, so it automatically

keeps all the conversation history per session, with no need of sending the last message as a reference. A ”session” is basically an assistant thread created at the beginning of the Pi control script, so the robot would recall everything that was told to him in that conversation. Each query to GPT only included the user prompt, since the system prompt is defined in the assistants workspace. Although, the robot can’t remember a previous conversation for when it was last used, since for every boot cycle, the assistant thread changes. This means that the robot doesn’t recall older conversations, just what was told to him in the current session. I could technically create an assistant thread manually and change the code so that only that one thread would be used for API calls, but that would mean that the token usage would increase, and the query time would take longer. Also, there is the extra cost for the calls, but that is not a big issue, since it would still be difficult to go over budget. The trade-off is the loss of conversation history (the robot can’t remember your name if you told it the last time you spoke with it), but I didn’t really find it a big problem, since the current conversation scope was more relevant. For future improvement, maintaining the context through all the conversations could make interactions smoother.

In conclusion, the software side is what makes the robot interactive. By using advanced AI models and focusing on the prompt engineering and protocol design, the resulting system successfully combines a cloud AI with a physical robot, despite some latency and simplicity of motion. The challenges encountered while designing the system made me aware of the importance of fail-safes when dealing with AI outputs, the need for programming the AI’s outputs for the robot, and the user experience details of interacting with a semi-autonomous robot. These conclusions will help improve the next versions of the system, as discussed in Chapter 5 and 6.

### 4 QUADRUPED ROBOT DESIGN AND CONTROL (HARDWARE)

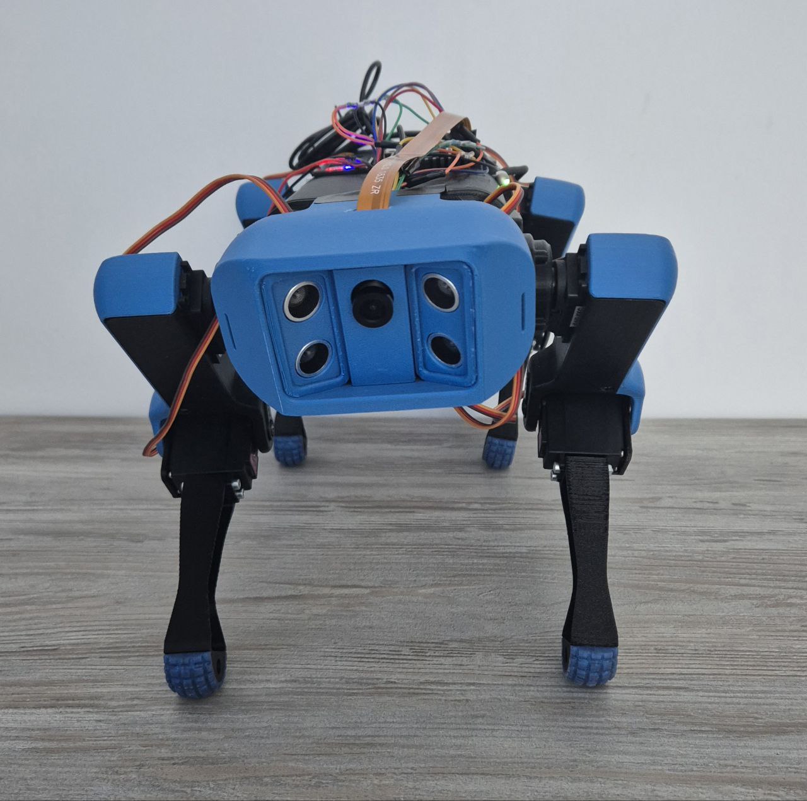
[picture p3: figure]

Figure 2: The finished robot, standing while waiting for a command

### 4.1 Mechanical Design and CAD Model:

The robot’s mechanical design is a quadruped structure, based on Boston Dynamics’ Spot (https://bostondynamics.com/products/spot/) and the open-source Spot Micro designs. (https://www.instructables.com/Nova-Spot-Micro-a-Spot-Mini-Clone/) Each leg has three segments (similar to the hip, thigh, and shin of an animal), that are moved by three servos, giving the robot 12 degrees of freedom in total. The design process involved two main tasks:

1. Obtaining the 3D models for the chassis and legs and modifying them for my specific usecase
2. Assembling the robot and calibrating the servos to provide the desired range of motion and stability

I started with existing CAD models from the internet. The frame of the robot is adapted from the project that started the SpotMicro community: KDY0523’s Spotmicro - robot dog, (https://www.thingiverse.com/thing:3445283) which provides the STL files (https://en.wikipedia.org/wiki/STL_(file_format)) for a miniaturized Spot clone that is designed to use 12 hobby-grade servos. (https://en.wikipedia.org/wiki/Servomotor) I imported these models into Autodesk Fusion 360 (https://www.autodesk.com/products/fusion-360/overview) to measure and modify them. The main modifications I made are:

1. Speaker Mount:

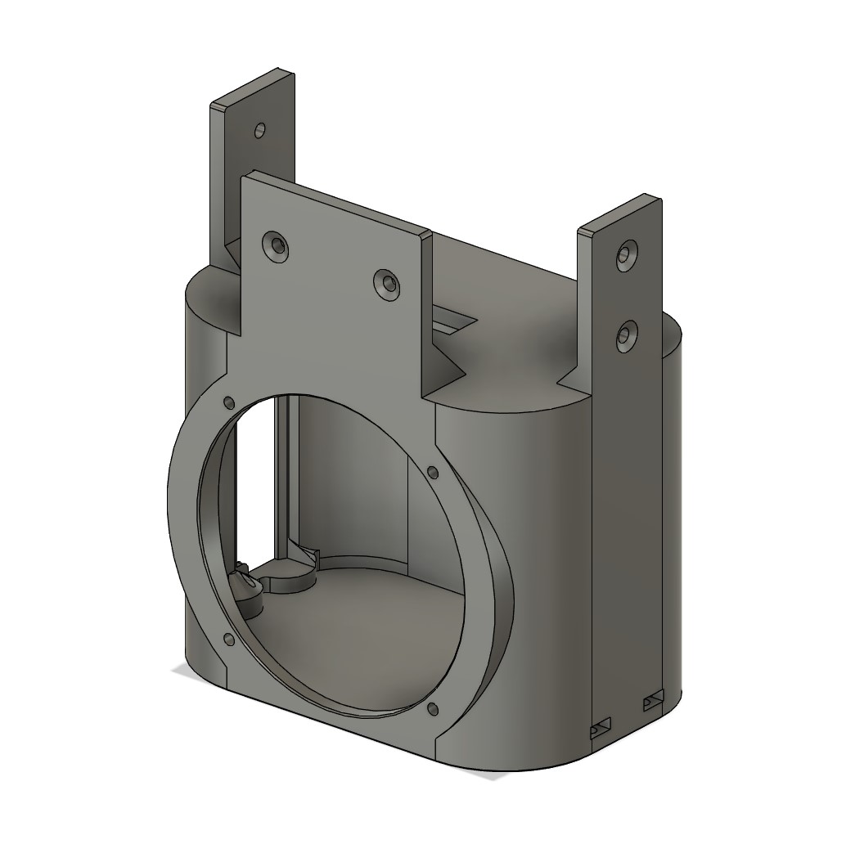
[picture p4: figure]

Figure 3: The designed 3D model for the speaker mount

For the robot to be able to respond to the user, it needed a speaker. I started from a Omega 5W portable speaker, (https://www.emag.ro/difuzor-portabil-fara-fir-pentru-dispozitive-mobile-omega-v4-2-tws-maro-deschis-og60w/pd/DC02PXMBM/) then disassembled it and saved the circuits. I sketched a rectangular box that would hold those parts and made it compatible with the robot’s front leg assemblies, so it could be mounted to them and act as the front half of the robot’s torso. To power the speaker, I used a MP2307DN buck converter, (https://www.emag.ro/set-10-x-convertor-descendente-ajustabil-retoo-bucking-step-down-mp2307dn-mini-360-cu-potentiometru-3a-4-5-23v-dc-dc-1-17v-e501/pd/DKG34VY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) and connected it to the Raspberry Pi via USB using an external audio card, (https://www.emag.ro/placa-de-sunet-usb-la-mini-jack-3-5-mm-adaptor-axroad-mall-plug-and-play-reducere-inteligenta-a-zgomotului-usor-de-folosit-pentru-casti-mi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) since the Raspberry Pi 5 doesn’t have a 3.5mm audio jack port.
This improvised speaker turned out to be effective, having the audio come straight from the robot. It did achieve quite a high volume, so there wouldn’t be any issues with users not hearing the robot.
To generate the robot’s response, as detailed in Chapter 3, I used the Espeak TTS library (https://espeak.sourceforge.net/) . I liked the retro and robotic sound of the voice, fitting for a robotic assistant.
2. Electronics Mount: This was a more difficult part to design. I needed something to connect to the speaker mount and the back legs, thus completing the robot body. I also needed to house the rest of the components that would make the robot work: the battery mount, the voltage regulator, the ampmeter, the Raspberry Pi, the Arduino Pro micro, and the PCA9685 module.
I placed the battery tray on the underside of the part, the voltage regulator on the side, leaving space for its heatsync and the Raspberry pi up top. The Arduino and the servo control module were seated in the remaining interior space, between the Pi and the battery.
After printing the mount, thankfully all parts fit in nicely and I was able to assemble the robot. The servo cables routed through the hole at the back and connected to the PCA9685 module, which was powered by the voltage regulator.

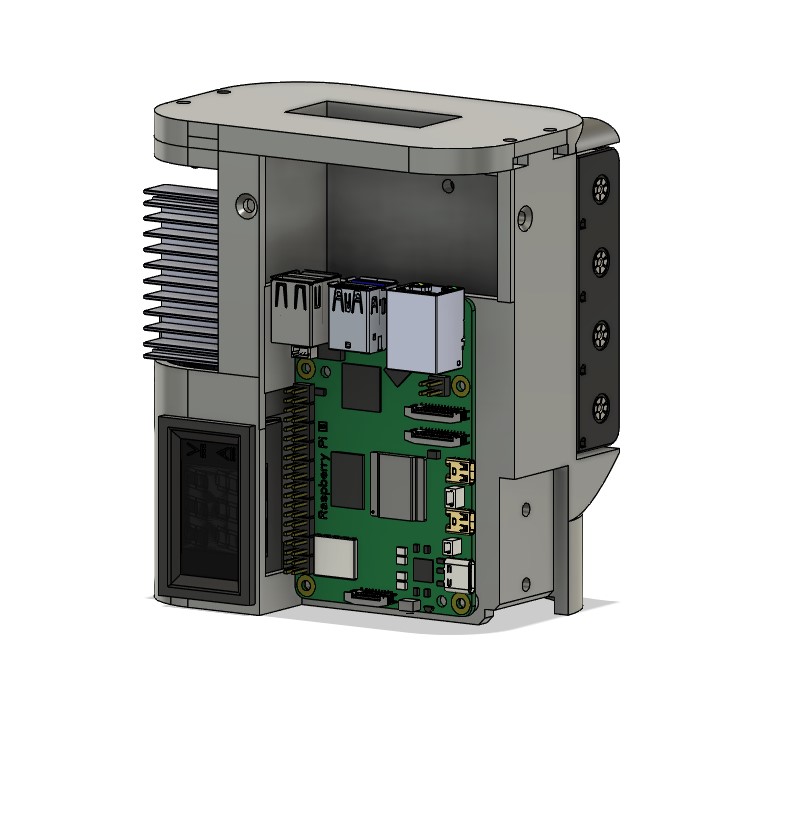
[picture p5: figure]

Figure 4: The designed 3D model for the electronics mount

3. Camera mount I wanted the camera to capture the front view of the robot. The front cover, which holds the ultrasonic distance sensors has an unused 25 mm wide space between the distance sensor mounts, the perfect space for the camera. I added 2 mounting holes to the underside of the cover, which I used to screw in the camera mount.
The model itself isn’t very complex, just a slanted profile to match the front cover angles, and a hole to pass the camera objective through.

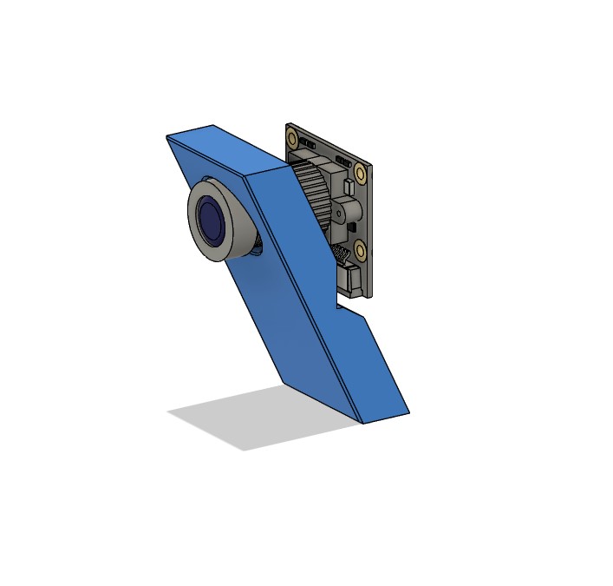
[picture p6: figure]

Figure 5: The designed 3D model for the camera mount

The parts were 3D-Printed[29] on my 2 machines: a Creality CR-10S Pro V2 (https://www.creality.com/products/cr-10s-pro-v2-3d-printer) and a Bambu Lab A1 Combo (https://eu.store.bambulab.com/products/a1?id=599117150694776844) using PLA (https://www.twi-global.com/technical-knowledge/faqs/what-is-pla) and PETG (https://all3dp.com/2/3d-printing-petg-comprehensive-guide/) filament at 15-20% infill with 0.4mm nozzles and 0.2 mm layer height. The structural parts (the black pieces of the legs and the torso) were printed from a combination of generic PLA (https://www.emag.ro/filament-pla-3dactive-1-75-mm-1100-g-negru-pla-1100-48043/pd/DYC4PB3BM/) and PETG, (https://www.emag.ro/filament-d-petg-easy-to-print-infix-1-75-mm-1-kg-220-260-c-negru-3/pd/DP942CYBM/) since I ran out of my PETG roll halfway through the printing process. The blue parts were printed in bambulab’s Matte blue PLA. (https://eu.store.bambulab.com/products/pla-matte?id=53926028673372) The total print time was around 40 hours for all the parts (torso parts, legs, brackets, mounts), but since I own 2 printers, I could print them in parallel, basically cutting the printing time by half. I encountered some typical 3D-printing issues, like holes not fitting screws perfectly and slight tolerance differences, but those were quickly solved with a drill and some sandpaper.

After printing the parts, I started assembling the components:

- Legs: Every leg assembly contains 3 segments: the tibia, which is the segment that

touches the ground and holds the knee servo, the hip, which is the middle segment, holding the hip flexing servo, and finally, the joint support for the last servo, the hip rotation actuator. Between the knee and hip servo there is an extra part, that supports the knee servo with a bearing.
- Front and back leg assemblies: Each leg assembly contains a left and right leg.

Those are held together by 2 supporting parts that act as a pelvis. (https://en.wikipedia.org/wiki/Pelvis)
- Torso: The robot’s torso is formed from the speaker and electronics mounts (detailed in Section 4.1). Those are the parts I designed to fit the custom electronics for this project. They use the existent mounting holes from the leg assemblies and interlock together using 6 M3 screws. When I was assembling the robot, I first had to install the electronics in their respective mounts (the speaker and electronics in the first part, and pretty much all of the electronics in the other), then slowly routed the leg servo cables from the leg assemblies through the parts, and into the servo control module.
- Front cover and camera mount: After completing the torso assembly, I moved to a

simpler one - the front cover assembly. Here, I first mounted the camera into its small support, then fastened it into the front cover, and added the distance sensors. I wired up the sensors and connected the camera ribbon cable, mounted the assembly in the front of the robot, and connected everything to the Raspberry.

One mechanical challenge was making sure that the robot could lift a leg without falling over, since the SpotMicro design is top-heavy, so the gait needs at least three legs on the ground at all times for stability. I did not implement dynamic balancing (e.g. by using a gyroscope), so the mechanical design has to ensure stability: I set the legs a bit wider by mounting the hip servos slightly to the exterior, and tuned their orientation further in the Arduino code. This small change helped with stability without affecting the walking process.

In conclusion, the mechanical design phase was a very important step in the making of this project. It required modifications and designing new parts from the ground up to accommodate my choice of hardware and ensure reliable operation. The result is a quadruped robot body that is capable of performing the movements ordered by the software while fitting all the electronics that give it full functionality.

### 4.2 Actuation: Servos and Kinematics

The movement of the robot is achieved with 12 servo motors arranged as described (3 per leg). These servos are standard RC (Radio Control) style servos that take a PWM (https://en.wikipedia.org/wiki/Pulse-width_modulation) signal to set an angle. I started with using the MG996R (https://towerpro.com.tw/product/mg996r/) (a popular low-cost metal gear servo), but they quickly proved to be sufficient for supporting the robot’s full weight. So, I ended up replacing most of the servos with the TD-8125MG (https://www.botnroll.com/en/servos/3655-metal-digital-servo-180-25kg-td-8125mg.html) model. Those really improved the motion of the robot. All servos run on 6V supplied from the battery via a 20A step-down regulator.

Servo characteristics: The MG996R and TD-8125MG servos both have approximately a 180 degree range, corresponding to a pulse width of 500-2500 µs, with 1500 µs as center (90 degrees). In practice, each servo’s actual range and center can vary slightly, and I calibrated them in the code by defining the servo offsets array (more details in Section 3.6). Their speed is about 0.2 seconds per 60 degrees at no load, but they’re slower under load. At first, when I started testing with the MG996R model, because of the robot’s weight, the knee servos in particular got overloaded when the robot was standing – they can hold the position but it draws significant current and they heat up if held for too long. Also, they can’t reach the standing position unassisted. Thankfully, using the TD-8125MG model mostly solved those problems.

PCA9685 servo driver: To control 12 servos, I ended up using the Adafruit 16-channel PWM driver board, (https://www.adafruit.com/product/815) based on the PCA9685 chip, which is connected to the Arduino via

I2C. (https://en.wikipedia.org/wiki/I%C2%B2C) This board generates 12-bit resolution PWM signals for all the servos without using the microcontroller’s timers, since the Arduino Pro Micro (Atmega32u4) (https://www.microchip.com/en-us/product/atmega32u4) has limited timers and could only directly control a few servos reliably. The PCA9685 acts as a hardware PWM controller: the Arduino sends it commands over I2C specifying channel and pulse width, and the chip handles the rest. As a result, the Arduino can send updates to servo positions and then continue with other logic while the PCA9685 continues outputting the required pulses. Another advantage is that it only uses two pins (SDA and SCL) to control all 12 servos, simplifying the wiring. I set the PCA9685 PWM frequency to 50 Hz, a typical value for servos (20 ms period). With 12-bit resolution, this gives pulse width increments of about 4 µs,

which is finer than the average hobby servo precision. I did not end up needing that fine of a resolution, but it is nice to have for future versions.

Kinematic configuration: Each leg’s kinematics can be described by two segments: thigh (upper segment) and shin (lower segment) and a base roll axis from the hip (to laterally move the leg). In the leg geometry, the thigh length is approximately 10.7 cm and the shin length is 13.4 cm (including the servo horn offsets). The default standing pose has both hip and knee at roughly 45 degree angles (0 degrees meaning the leg is fully extended straight down). In that pose, the foot is about 15-16 cm below the hip horizontally, giving the robot a standing height of around 16 cm, and a total height of approximately 23 cm including the body.

Gait Implementation: I decided to use a parallel gait for walking, where one leg moves at a time while the other three remain on the ground to support the robot. This gait is pretty stable if the center of mass stays in the triangle of support. The sequence is: lift front-left leg, move it forward, put it down, then rear-right leg, move it forward, put it down, and the same for the front-right and rear-left. After one cycle, the robot has moved forward. The turning gaits also only use one leg per movement to remain stable, but instead of advancing all the legs in the same direction, they reverse the directions for the diagonal legs to make the robot rotate (more details about the gaits and code in Section 3.6).

During testing, the TD-8125MG servos handled the load, but did get warm, especially the hip and knee servos after walking. This was expected, and thankfully they never overheated. The 3D models included supporting bearings on the knee joints and the lateral rotation of the hip, but none for the forward hip servo, where the whole leg was held only by the servo horn. In my case this didn’t affect the movement, but in future versions additional support for the hip would be recommended.

### 4.3 Electronic Architecture

This project, being this hardware intensive, needed a complex electronic architecture. The whole robot is powered by a 4-cell battery, situated in the back half of the torso. This battery then feeds the 3 voltage regulators, used for the servos, the Raspberry Pi and the speaker. The Arduino is powered directly from the Raspberry via a usb cable, and the Pi is connected to a 65W quick charge module (https://www.emag.ro/modul-incarcare-rapida-pd65w-cu-interfata-type-c-pd3-1-qc3-0-8-30v-dc-2-5mm-rx566/pd/DN7XBQYBM/) that is powered directly from the battery. The speaker is connected to the pi using an external audio card. (https://www.emag.ro/placa-de-sunet-usb-la-mini-jack-3-5-mm-adaptor-axroad-mall-plug-and-play-reducere-inteligenta-a-zgomotului-usor-de-folosit-pentru-casti-mi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)

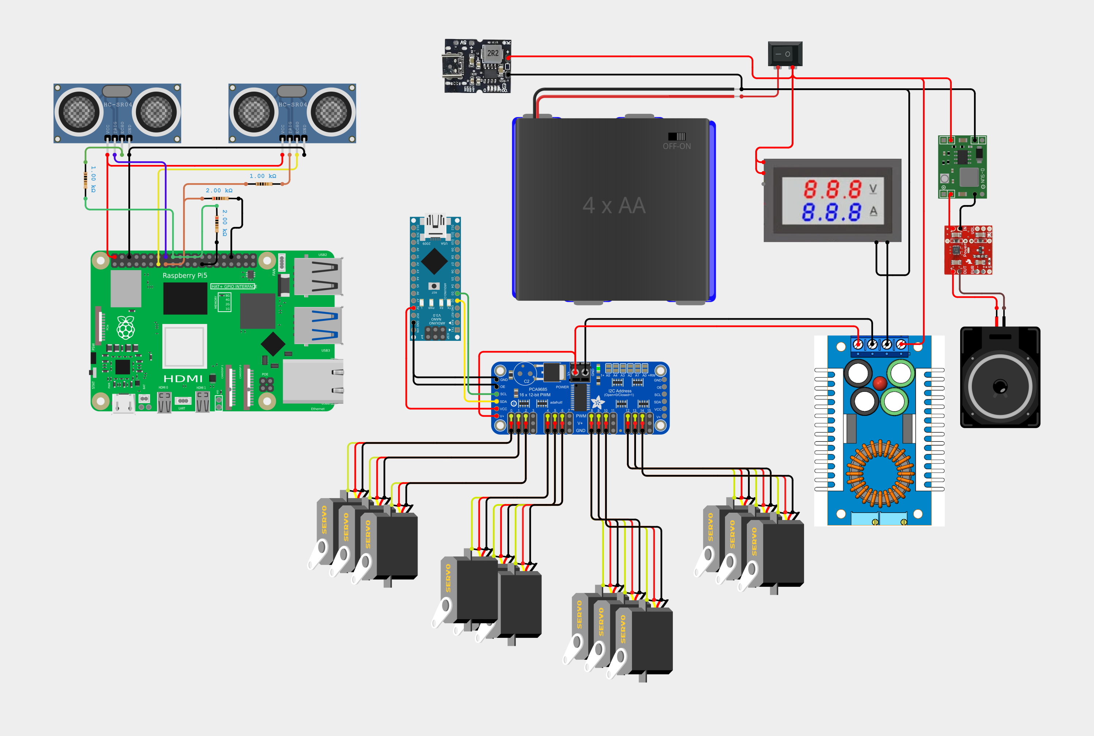
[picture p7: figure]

Figure 6: The wiring diagram for the project

Power Considerations: The robot is powered by a 4-cell 2200 mAh 18650 (https://en.wikipedia.org/wiki/18650_battery) battery pack. The individual cells are mounted in a 4x case. (https://ardushop.ro/en/cases-and-boxes/948-4x-18650-battery-holder-6427854012692.html) Running 12 servos simultaneously can draw a lot of current (a MG996R or TD-8125MG servo have stall power draws upwards of 2 A). To power them I used a 20A YD4020J (https://www.emag.ro/modul-sursa-de-coborare-tensiune-general-300w-20a-6-40vdc-gd-0032/pd/DYWYV8YBM/) regulator set to output 6V. It is wired directly into the PCA9685 board, using the power input terminal blocks. This feeds all the servos, greatly simplifying the wiring. The speaker and raspberry used separate voltage regulators as to not consume the servomotors’ power budget.

### 4.4 Arduino Firmware for Motion Control

The Arduino Pro Micro runs a program that interprets incoming serial commands and executes the corresponding motion sequences using the servos. It was written in Arduino C and structured to handle the different named actions. The main parts of the firmware are:

1. Serial command parsing (as described in Section 3.5): The Arduino is connected to the Pi via a USB cable, so it gets directly powered by the Raspberry, while using the same cable for Serial communication. The program runs a simple line parser in the loop to read the received commands.
2. Movement routines for each action: After the microcontroller receives a movement command and the number of steps for it, it executes the corresponding movement function for it, thus signaling to the servos to move in the desired direction. As explained in Section 4.2, I used a PCA9685 (https://www.adafruit.com/product/815) board to control the servos. It mostly helped on wiring, since it also supplied every servo with the connected power from the voltage regulator, so it reduced the need for power and signal cables to each servo. It was also simple to wire it up to the Arduino, since it used the I2C protocol, (https://en.wikipedia.org/wiki/I%C2%B2C) and only needed 6 pins connected.

In this project, the Arduino was only responsible for the movement of the servos, so it didn’t have any sensors connected. It worked well for this scope, but in future versions, adding a gyroscope (https://corporate.epson/en/technology/search-by-products/microdevice/gyro-sensor.html) or an accelerometer (https://en.wikipedia.org/wiki/Accelerometer) to help with uneven terrain and fall detection would be a good upgrade to the system, since any slope or uneven step could trip it. All the tests were conducted on a flat floor. I didn’t test outside or on rough terrain. The design can walk on carpets and wood flooring.

### 4.5 Sensor Integration and On-board Processing

Although the microcontroller didn’t have any sensors connected, this wasn’t the case for the Pi, as it had the following sensors attached:

1. The Distance Sensors: The robot has 2 Ultrasonic HC-SR04 (https://www.sparkfun.com/ultrasonic-distance-sensor-hc-sr04.html) distance sensors, which are used to gather more information about the potential obstacles in its proximity. They are mounted in the front of the robot, on one side and the other of the camera (which is positioned in the middle), and at a 50 degrees interior angle. This means that, for example, the right sensor detect the obstacles in the front-left side of the robot. The Pi runs a simple distance detection command on each sensor(by sending a 10 µs pulse and measuring the time it takes to return), and sends them to the assistant API, together with the user prompt and camera picture.
2. The Camera: The Pi camera is mounted in the front of the robot, where his ”head” is. It is held in by the camera mount part that I designed in Fusion (detailed in Section 4.1). It uses a ribbon cable (https://www.raspberrypi.com/products/camera-cable/) for the connection to the Pi’s camera port, and it is directly controlled by the Raspberry using the libcamera (https://github.com/raspberrypi/libcamera) library.
3. Microphone and Speaker: To record audio reliably, I used this wireless lavalier microphone (https://www.aliexpress.com/item/1005006802619837.html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) I got from Aliexpress for cheap. It proved to be a great choice, since the range is good (up to 10 meters) and the audio quality doesn’t affect Whisper’s transcription. The fact that it’s wireless also meant that the audio recording would work better, since a microphone mounted on the robot would add extra noise from the servo hum and have the user follow the robot and try to speak directly at it, instead of just holding the wireless microphone. And for the audio output (so that the robot can speak via TTS), I used a 5W portable speaker. (https://www.emag.ro/difuzor-portabil-fara-fir-pentru-dispozitive-mobile-omega-v4-2-tws-maro-deschis-og60w/pd/DC02PXMBM/) I removed its internals and transplanted them into the speaker mount (explained in Section 4.1).

In summary, the sensor integration was straightforward for voice and obstacle sensing. The ultrasonic sensors were used to inform the AI’s decisions, alongside the camera view, demonstrating how some simple sensors can make an AI-driven robot more grounded in reality, preventing ”mindless” instruction following.

### 4.6 Physical Control Challenges and Tuning

During building and testing of the robot, I encountered a couple issues that needed to be fixed:

1. Servo Calibration and Alignment: Although I set every servo to its middle position while mounting the legs using a servo tester, (https://ardushop.ro/ro/unelte/540-tester-servomotoare-6427854006301.html?gQT=1) so all the legs would sit in the standing position when the robot would get powered up, some of them (due to the manufacturing or the way I assembled the joints) moved to different positions. This issue was quickly fixed by introducing a servo offset array in the Arduino code to slightly adjust each actuator’s angle (code snippet in Section 3.6).
2. Thermal Issues: As expected, after a couple of minutes of use, the servos would start heating up, due to the load of keeping the robot standing. The temperature would slowly rise, but stabilise eventually. The servos got warm, but not burning hot, so about 50 degrees Celsius. It’s a good thing they stopped there, since the materials I used to 3D-print the legs (PLA and PETG) start softewning above 60 degrees Celsius. Thankfully, the servo temperatures didn’t pose a significant problem to this project, but for a future version it would be a great idea to add some heat syncs top the servos, or even some active cooling to keep them at lower temperatures.
3. Power issues: This was also a persistent issue for the project: The YD4020J, (https://www.emag.ro/modul-sursa-de-coborare-tensiune-general-300w-20a-6-40vdc-gd-0032/pd/DYWYV8YBM/) although rated for 20A, only put out around 15A max. This was fine for the most part, but in specific motions where all the legs would have to move at the same time (for example when the robot stand up straight after lying on the floor), the servos had a bigger power draw, which made the regulator voltage drop down 1-2 V . A reliable fix for this issue in future versions would be to use a more powerful regulator, or to add additional regulators to increase the power budget. I instead tuned the gaits and the motions to only ever use 2 feet at the same time, to reduce the load. This fixed the power draw issues, but it was more of a workaround than a fix.
4. Noise and Wear: Upon powering up the robot, the first thing that a user hears is the servo whine, caused by the actuator trying to hold its position. This is generally unavoidable, since any type of servo produces a buzzing sound when under load. More expensive models do emit less noise, but aren’t silent either. This doesn’t pose an issue for this project’s scope, but for a commercial version this might annoy some users. This could be fixed by upgraded actuators or a structural redesign. Another more significant issue could be the wear on the components. In my testing, and since the robot wasn’t built too long ago, I didn’t observe wear on any component except the old MG996R servos I used in the first version. But, after changing over to the TD-8125MG model, I didn’t notice any wear or degrading performance. This is due to the higher build quality and torque spec of the servos.

Overall, the physical tuning of the robot was an iterative process: I went back and forth between adjusting the servos and joints, to adjusting the control code. I even adjusted the AI prompt a couple of times to change the robot’s capabilities and range of movements.

The physical part of this project taught me a lot about servomotors, power delivery circuitry, battery configurations, and most importantly, the inner workings of walking robots.

### 5 EXPERIMENTAL RESULTS AND DISCUSSION

### 5.1 Example Interaction Scenario

To evaluate the integrated system, I conducted a series of test interactions that simulate how a user might interact with the robot. A representative scenario is the following (a full conversation can be found in Appendix B):

I start by saying, ”Hello robot!” to the robot. The robot’s microphone records this, Whisper transcribes it as ”Hello robot!”, and the text is sent to GPT-4 along with the sensor data (e.g. the ultrasonic sensors detect distances over 50 cm, so no immediate obstacle) and the camera feed. The GPT assistant processes the image, sensor data and camera picture, recognizes a human (me) in the picture, and responds in a friendly manner with the greeting motion. It returns this JSON:

{
"movement": "greet",
"steps": "0",
"speech": "Hello, there! How can I help?" }

The Raspberry Pi parses this and sends the speech to the TTS system and the commands over to the Arduino. The robot’s speaker outputs the voice audio, while the servos start moving in the predefined position. This greeting move is coded to have the robot sit on his hind legs, lift its left arm and wave it a few times, returning to the sitting position afterwards.

Next, I ask the robot to walk forward - ”Can you walk forward, please?” The transcription still picks this up, despite the background noise recorded by the microphone from the servos, giving us ”Can you walk forward, please?”. The assistant receives this, plus sensor data (there is enough space for the robot to move) and a picture of the room he is in, with plenty of space to explore, and me staying in the center. The assistant understands it as an instruction to start walking. It responds with:

{
"movement": "forward",
"steps": "3",
"speech": "Sure, I will walk forward." }

The Pi speaks ”Sure, I will walk forward.” through the speaker and sends the ”forward” command to Arduino. The Arduino executes the walking gait sequence 3 times. The robot rises from its sitting position and moves forward a for 6 steps (a movement gait does 2 steps, one for the right legs and one for the left legs - so 30 cm forward in total). This takes about 15 seconds to complete. The robot starts to move towards me. At the end of the gait, the Arduino sends a ”Finished instruction” string, which the Pi uses to know that it finished moving.

Next, I added a box in the front right of the robot, to test its pathfinding, and said ”Continue going forward”. Like before, the transcription was accurate and the assistant got the instruction to move forward. But because it detected the box as an obstacle via the left distance sensor (which is facing right) and into the camera view, the reply was a solution to the problem:

{
"movement": "left",
"steps": "3",
"speech": "I detect something in front of me. I cannot move forward safely. I am turning left to avoid the obstacle"
}

The robot replies and starts turning in place. This motion takes 5 seconds to rotate approximately 15 degrees and the LLM requested 3 steps, so after 15 seconds, the robot now faces a new direction, away from the box, 45 degrees to the left.

The back and forth would continue like this, and when there would be no instructions from the user (I wouldn’t say anything in the microphone), the robot would either ask if I wanted it to continue going forward and stand in place, or just try to ask for a new command. He occasionally turns for 1-3 steps to look towards a person in the room when deprived of commands.

I also tried to test the Whisper transcription capabilities by speaking gibberish or too quietly into the microphone. This resulted in some random words at times, or empty transcriptions. These prompted the robot to ask for clarifications:

{
"movement": "stand",
"steps": "0",
"speech": "I’m sorry, but I didn’t understand your command. Could you please repeat it?
}

I even tried speaking to the robot in Romanian, since I am running Whisper in translation mode, and it ended up transcribing correctly in those cases as well.

These test conversations helped me observe the following:

- Speech Recognition Accuracy: Whisper returned correct transcriptions consistently

for my speech. Even multi-part commands like ”come here, walk forward” were transcribed with all key words intact. This high accuracy is important, because any misinterpretation could make GPT misunderstand the instruction (e.g. ”turn left” misinterpreted as ”turn that” wouldn’t make much sense).
- GPT Understanding and Reasoning: GPT-4 interpreted my intent well, including

direct commands, questions, and complex sentences. It followed JSON format well. I didn’t observe format errors after the prompt was refined. It also made reasonable decisions with sensor data – refusing to go forward when an obstacle was detected. It matched my expectations well.
- Physical Execution: The executed movements matched the commands. The forward

movement was sluggish because of the cheaper servos I first used, but it still got there. The turns are harder since they need balancing, but the robot did indeed turn in the desired direction. A good thing is that the robot did not fall during these actions, especially after changing to the more powerful servos. There were some oscillations when a leg lifted due to the low quality of the servos, but that was again solved by replacing them with better ones. The obstacle avoidance test worked – the robot did not move further forward when the box was placed in path, and verbally acknowledged the obstacle. That is a good demonstration of integrating perception into decision-making, which many simple robots lack.
- Latency: I measured the delays in this scenario: the initial greeting took 5s from end of the speech recording to the robot’s reply (Whisper - 1.5s, GPT - 3.5s). Movement commands took longer mainly due to movement time, not processing. For example, after ”walk forward”, the voice reply came in 5s, then movement took 15s. This is due to the way the movement gait is written. For the Continue going forward” command that was refused, it was 6s to reply. I didn’t get bothered by those delays, but adding 5 more seconds would’ve made the robot seem slow, users would get bored. So keeping interactions short and the robot giving some sign it’s processing (even a small LED blinking on robot) would helpful. I didn’t implement anything other than the speech to signal to the user that the robot is processing the information.
- Error Handling: When I purposefully tried to break the transcription: e.g. mumbling or gibberish, Whisper might return ”[inaudible]” or some random words. Thanks to the prompt though, GPT replied that it didn’t understand and ask for a new command. When I treid speaking clearly in another language, the transcription worked well. This system could be improved to detect if Whisper has low confidence and then it would ask the user to repeat. I didn’t implement that, but it is a good idea for future work.
- Conversation memory: Since I used the assistants API, the AI has access to the

conversation history, so no context was lost. It can’t remember other conversations due to the thread change though, so when the robot is restarted it starts fresh, with no conversation history, just the system prompt. This didn’t represent a problem, but it would be interesting to implement lasting memory in future versions.

The example scenario confirmed the core functionality: the pipeline for voice command to action works well, and the robot can integrate dialogue with movement. When tested with friends, they quickly started personifying the robot, so it ended with good feedback. This shows the project’s goal of creating an interactive robot companion was mostly completed.
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

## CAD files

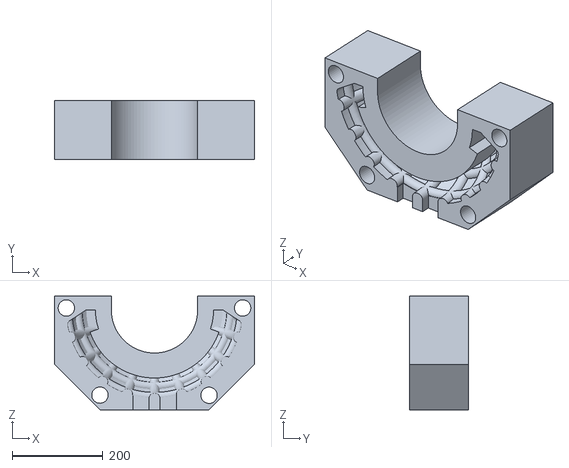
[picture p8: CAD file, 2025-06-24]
3d_models/foot_mold_right.stl
440.0 x 130.0 x 250.0

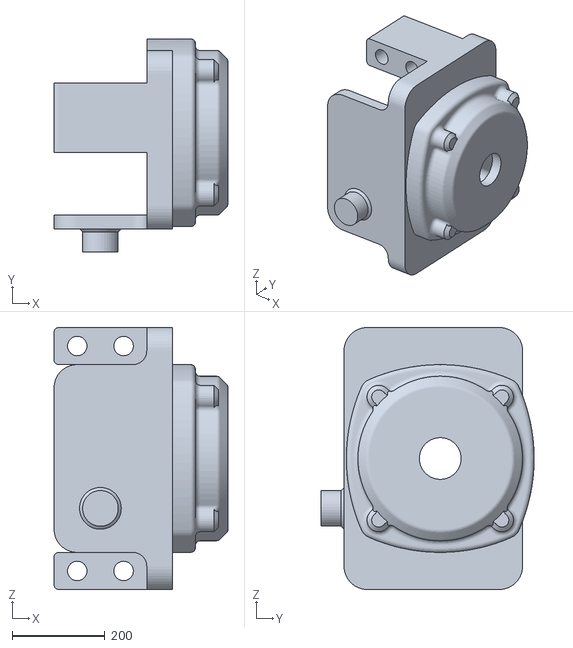
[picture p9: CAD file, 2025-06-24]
3d_models/L_arm_joint_mg_8mm.stl
375.0 x 460.0 x 565.0

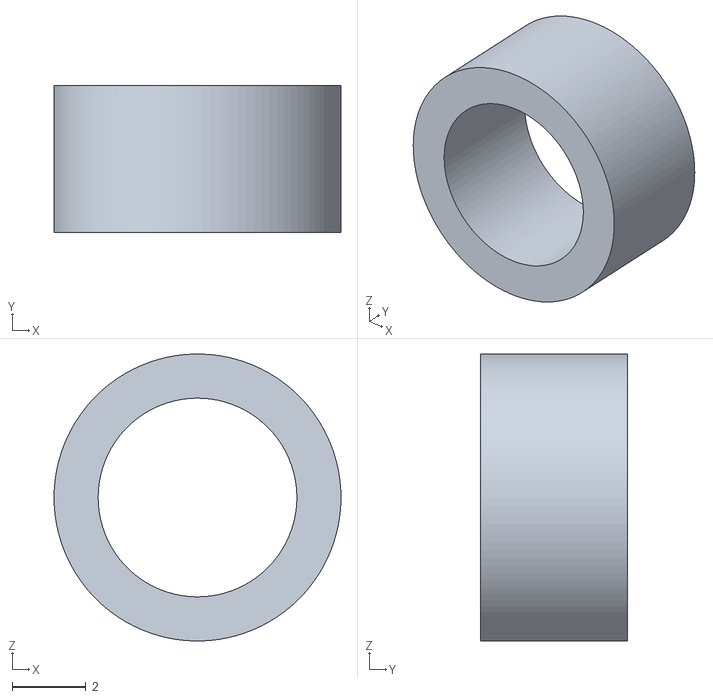
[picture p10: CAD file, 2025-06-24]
3d_models/Bearing_adapter.stl
7.80 x 4.00 x 7.80

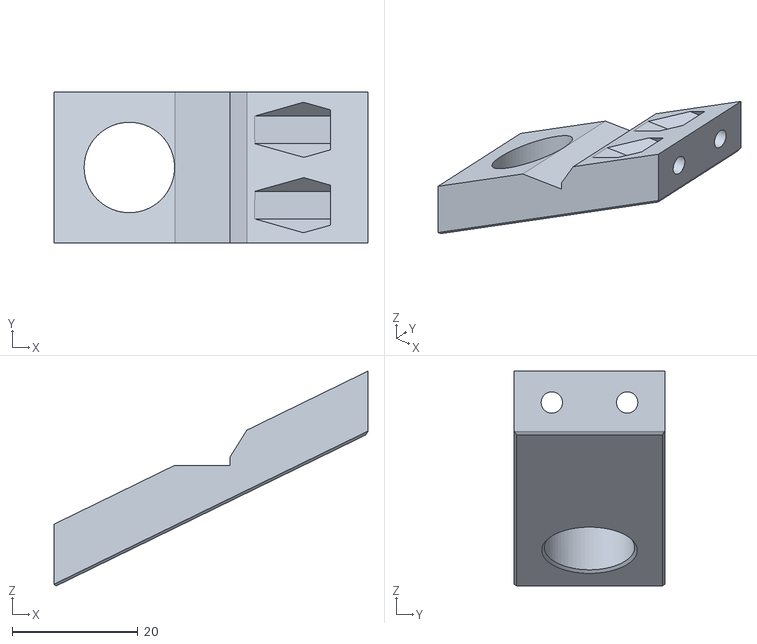
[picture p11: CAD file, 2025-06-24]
3d_models/Camera_mount.stl
50.0 x 24.0 x 34.2

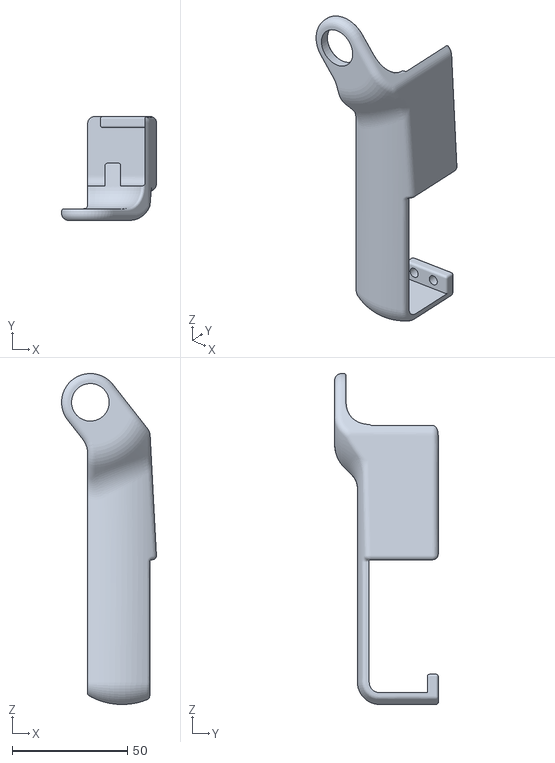
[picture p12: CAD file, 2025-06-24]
3d_models/R_arm_cover.stl
41.2 x 45.0 x 143.5

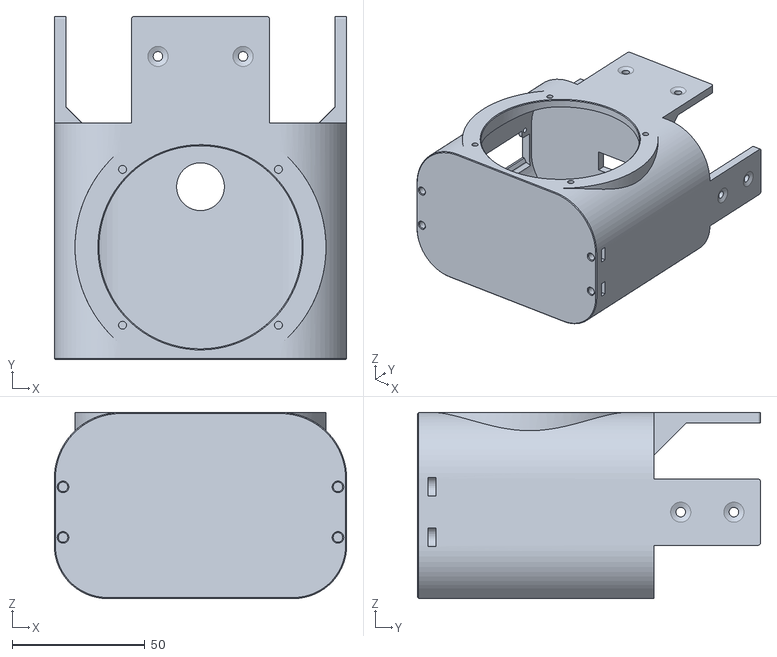
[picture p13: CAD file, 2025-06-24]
3d_models/Nova_sound_box.stl
110.0 x 129.0 x 70.0

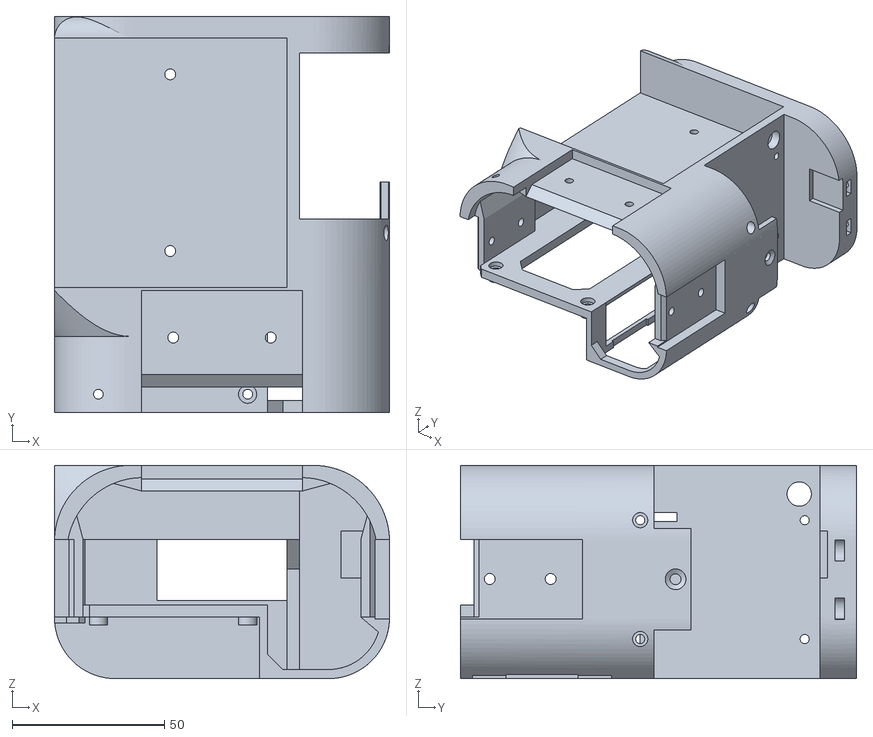
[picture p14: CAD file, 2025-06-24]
3d_models/Electronics_mount.stl
110.0 x 130.0 x 70.0

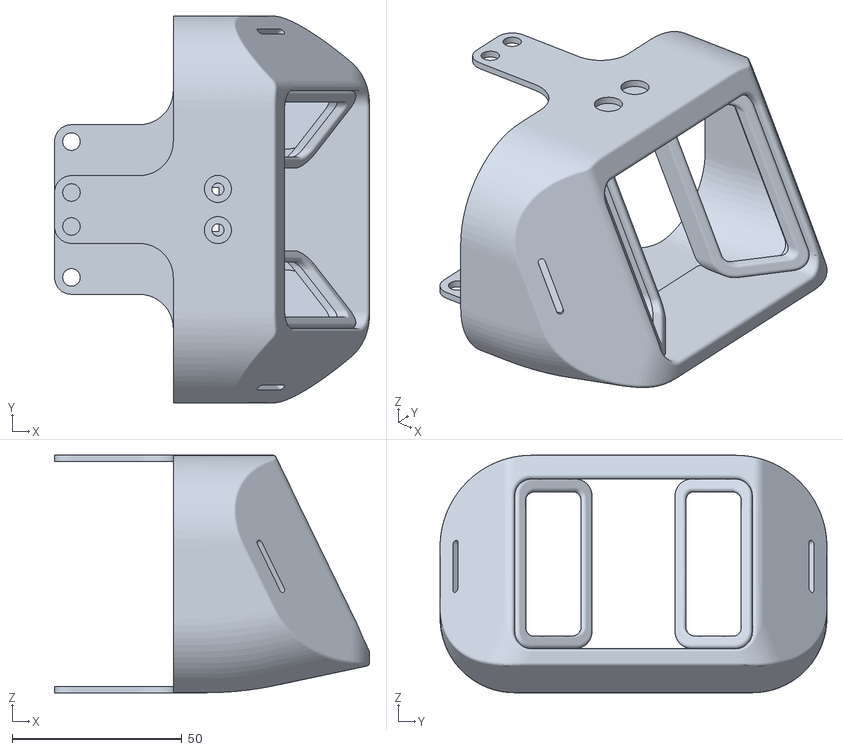
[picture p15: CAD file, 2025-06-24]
3d_models/Front_cover.stl
92.8 x 114.0 x 70.0

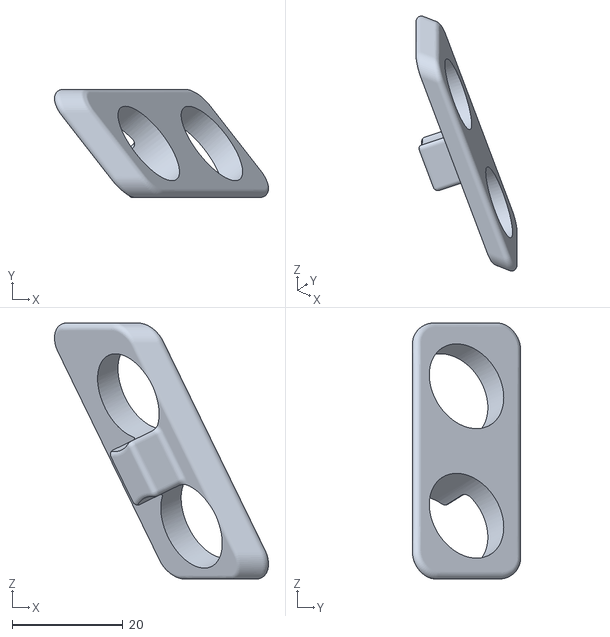
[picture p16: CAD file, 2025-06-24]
3d_models/L_ultra_sonic.stl
38.6 x 19.5 x 46.2

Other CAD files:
3d_models/foot_mold_left.stl
3d_models/R_arm_joint_mg_8mm.stl
3d_models/L_arm_cover.stl
3d_models/R_ultra_sonic.stl

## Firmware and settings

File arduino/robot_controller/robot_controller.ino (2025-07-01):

#include <Wire.h>
#include <Adafruit_PWMServoDriver.h>

// PCA9686 setup
Adafruit_PWMServoDriver pwm = Adafruit_PWMServoDriver();
const uint16_t SERVOMIN = 150;    // pulse for 0°
const uint16_t SERVOMAX = 600;    // pulse for 180°
const uint8_t NUM_SERVOS = 18;

// Each leg: [hip, shoulder, elbow]
const uint8_t legServos[4][3] = {
  {0, 1, 2},   // FL
  {3, 5, 6},   // FR
  {8, 9, 10},   // RL
  {12, 13, 14}  // RR
};

// The offsets for each leg servo
uint8_t legOffsetsCrouched[4][3] = {
  {40, 50, 65},  // FL
  {100, 90, 80},  // FR
  {60, 100, 90},  // RL
  {80, 60, 70}   // RR
};

// The offsets for each leg servo
uint8_t legOffsets[4][3] = {
  {90, 70, 65},  // FL
  {50, 70, 80},  // FR
  {90, 90, 90},  // RL
  {50, 70, 70}   // RR
};

uint8_t currentAngles[NUM_SERVOS] = {0, 15, 65, 140, 0, 130, 80, 0, 0, 140, 80, 0, 140, 10, 70};  // Stores current angle for each servo

// Map angle to PWM pulse
uint16_t angleToPulse(uint8_t angle) {
  return map(angle, 0, 180, SERVOMIN, SERVOMAX);
}

// Move a servo to its target angle smoothly
void sweepServoToAngle(uint8_t servoIndex, uint8_t targetAngle, int duration_ms) {
  uint8_t current = currentAngles[servoIndex];
  int stepCount = abs(targetAngle - current);
  if (stepCount == 0) return;

  int stepDelay = duration_ms / stepCount;
  int direction = (targetAngle > current) ? 1 : -1;

  for (int angle = current; angle != targetAngle; angle += direction) {
    pwm.setPWM(servoIndex, 0, angleToPulse(angle));
    delay(stepDelay);
  }
  pwm.setPWM(servoIndex, 0, angleToPulse(targetAngle));  // Ensure exact final position
  currentAngles[servoIndex] = targetAngle;  // Update tracker
}

// Directly set absolute servo angles for one leg
void setLegDirectAngles(uint8_t legIndex, uint8_t hipAng, uint8_t shAng, uint8_t elAng) {
  pwm.setPWM(legServos[legIndex][0], 0, angleToPulse(hipAng));
  pwm.setPWM(legServos[legIndex][1], 0, angleToPulse(shAng));
  pwm.setPWM(legServos[legIndex][2], 0, angleToPulse(elAng));

  int id = legIndex * 4;

  currentAngles[id] = hipAng;
  currentAngles[id + 1] = shAng;
  currentAngles[id + 2] = elAng;

}

// Set servo angles for one leg using the sweeping function
void setLegAngles(uint8_t legIndex, uint8_t hipAng, uint8_t shAng, uint8_t elAng, int duration_ms = 100) {
  sweepServoToAngle(legServos[legIndex][0], hipAng, duration_ms);
  sweepServoToAngle(legServos[legIndex][1], shAng, duration_ms);
  sweepServoToAngle(legServos[legIndex][2], elAng, duration_ms);
}

// Set servo angles relative to per-leg offsets
void setLegRelativeAngles(uint8_t legIndex, int8_t hipDelta, int8_t shDelta, int8_t elDelta) { // They start off from the stasnding position
  setLegAngles(
    legIndex,
    constrain(legOffsets[legIndex][0] + hipDelta, 0, 180),
    constrain(legOffsets[legIndex][1] + shDelta, 0, 180),
    constrain(legOffsets[legIndex][2] + elDelta, 0, 180)
  );
}

void standPosition() {
  Serial.println("Standing still.");

  for (int i = 0; i < 4; i++) {
    setLegAngles(i,
      legOffsets[i][0],
      legOffsets[i][1],
      legOffsets[i][2]
    );
  }

  delay(100);
}

void crouchPosition() {
  Serial.println("Crouching.");

  for (int i = 0; i < 4; i++) {
    setLegAngles(i,
      legOffsetsCrouched[i][0],
      legOffsetsCrouched[i][1],
      legOffsetsCrouched[i][2]
    );
  }

  delay(100);
}

void powerUpPosition() {

  setLegDirectAngles(0, currentAngles[0], currentAngles[1], currentAngles[2]);
  setLegDirectAngles(1, currentAngles[4], currentAngles[5], currentAngles[6]);

  delay(1000);

  setLegDirectAngles(2, currentAngles[8], currentAngles[9], currentAngles[10]);
  setLegDirectAngles(3, currentAngles[12], currentAngles[13], currentAngles[14]);

  delay(100);
}

void layFlatPosition() {      // Set all the legs in their crouched position
  crouchPosition();           // Added a buffer position
  delay(100);
  
  Serial.println("Laying flat.");

  setLegAngles(0, 0, 15, 65);     //FL
  setLegAngles(1, 140, 130, 80);  //FR
  setLegAngles(2, 0, 140, 80);    //RL
  setLegAngles(3, 140, 10, 70);   //RR

  delay(1000);
}

void sitPosition() {          // The front legs are in the standing position, and the back ones are crouching
  crouchPosition();           // Added a buffer position
  delay(100);
  
  Serial.println("Sitting.");

  setLegAngles(0, 50, 50, 65);    //FL
  setLegAngles(1, 90, 90, 80);    //FR
  setLegAngles(2, 0, 140, 80);    //RL
  setLegAngles(3, 140, 10, 70);   //RR

  delay(1000);
}

void pawPosition() {          // Same as sitting, but with the left foot stretched
  crouchPosition();           // Added a buffer position
  delay(100);
  
  Serial.println("Holding paw.");

  setLegAngles(2, 0, 140, 80);    //RL
  setLegAngles(3, 140, 10, 70);   //RR
  setLegAngles(1, 100, 90, 65);   //FR
  setLegAngles(0, 120, 140, 75);  //FL

  delay(1000);
}

void salutePosition() {          // Same as the paw position, but also waving
  crouchPosition();           // Added a buffer position
  delay(100);
  
  Serial.println("Greeting.");

  setLegAngles(2, 0, 140, 80);    //RL
  setLegAngles(3, 140, 10, 70);   //RR
  setLegAngles(1, 100, 90, 65);   //FR
  setLegAngles(0, 120, 140, 75);  //FL

  delay(200);

  setLegAngles(0, 120, 140, 75);  //FL
  delay(100);
  setLegAngles(0, 100, 140, 75);  //FL
  delay(100);
  setLegAngles(0, 130, 140, 75);  //FL
  delay(100);
  setLegAngles(0, 100, 140, 75);  //FL
  delay(100);
  setLegAngles(0, 130, 140, 75);  //FL

  delay(1000);

  setLegAngles(0, 50, 50, 65);    //FL
  setLegAngles(1, 90, 90, 80);    //FR
}

void stepForwardCycle() {
  // Phase 1: Lift FL
  setLegRelativeAngles(0, -10, -10, -10);
  delay(100);

  // Phase 2: Swing FL forward
  setLegRelativeAngles(0, -10, 20, 0);
  delay(100);

  // Phase 3: Place FL down
  setLegRelativeAngles(0, 10, 20, 0);
  delay(100);

  // Phase 4: Lift FR
  setLegRelativeAngles(1, 10, 10, 10);
  delay(100);

  // Phase 5: Swing FR forward
  setLegRelativeAngles(1, 10, -20, 0);
  delay(100);

  // Phase 6: Place FR down
  setLegRelativeAngles(1, -10, -20, 0);
  delay(100);

  // Phase 7: Drag FR + FL + RR + RL backward
  setLegRelativeAngles(0, 0, 0, 0);
  setLegRelativeAngles(1, 0, 0, 0);
  setLegRelativeAngles(2, 20, 15, 0);
  setLegRelativeAngles(3, -20, -15, 0);
  delay(100);

  // Phase 8: Lift RR
  setLegRelativeAngles(3, 20, -15, -10);
  delay(100);

  // Phase 9: Place RR down
  setLegRelativeAngles(3, 0, 0, 0);
  delay(100);

  // Phase 10: Lift RL
  setLegRelativeAngles(2, -20, 15, 10);
  delay(100);

  // Phase 11: Place RL down
  setLegRelativeAngles(2, 0, 0, 0);
  delay(100);

}

void stepBackwardCycle() {
  // Phase 1: Lift FL
  setLegRelativeAngles(0, -10, -10, -10);
  delay(100);

  // Phase 2: Swing FL backward
  setLegRelativeAngles(0, -10, -20, 0);
  delay(100);

  // Phase 3: Place FL down
  setLegRelativeAngles(0, 10, -20, 0);
  delay(100);

  // Phase 4: Lift FR
  setLegRelativeAngles(1, 10, 10, 10);
  delay(100);

  // Phase 5: Swing FR backward
  setLegRelativeAngles(1, 10, 20, 0);
  delay(100);

  // Phase 6: Place FR down
  setLegRelativeAngles(1, -10, 20, 0);
  delay(100);

  // Phase 7: Drag FR + FL + RR + RL forward
  setLegRelativeAngles(0, 0, 0, 0);
  setLegRelativeAngles(1, 0, 0, 0);
  setLegRelativeAngles(2, -20, -15, 0);
  setLegRelativeAngles(3, 20, 15, 0);
  delay(100);

  // Phase 8: Lift RR
  setLegRelativeAngles(3, -20, 15, -10);
  delay(100);

  // Phase 9: Place RR down
  setLegRelativeAngles(3, 0, 0, 0);
  delay(100);

  // Phase 10: Lift RL
  setLegRelativeAngles(2, 20, -15, 10);
  delay(100);

  // Phase 11: Place RL down
  setLegRelativeAngles(2, 0, 0, 0);
  delay(100);
}

void turnRightCycle() {
  // Phase 1: Lift FR
  setLegRelativeAngles(1, 10, 10, 20);
  delay(100);

  // Phase 2: Place FR down
  setLegRelativeAngles(1, 0, 0, 10);
  delay(100);

  // Phase 3: Lift FL
  setLegRelativeAngles(0, -20, -15, 10);
  delay(100);

  // Phase 4: Place FL down
  setLegRelativeAngles(0, 0, 0, 10);
  delay(100);

  // Phase 5: Drag FL + FR left
  setLegRelativeAngles(0, 0, 0, 0);
  setLegRelativeAngles(1, 0, 0, 0);
  delay(100);

  // Phase 6: Lift RR
  setLegRelativeAngles(3, 20, -15, -10);
  delay(100);

  // Phase 7: Place RR down
  setLegRelativeAngles(3, 0, 0, 0);
  delay(100);

  // Phase 8: Lift RL
  setLegRelativeAngles(2, -20, 15, 10);
  delay(100);

  // Phase 9: Place RL down
  setLegRelativeAngles(2, 0, 0, 0);
  delay(100);
}

void turnLeftCycle() {
  // Phase 1: Lift FL
  setLegRelativeAngles(0, -10, -10, -20);
  delay(100);

  // Phase 2: Place FL down
  setLegRelativeAngles(0, 0, 0, -10);
  delay(100);
  
  // Phase 3: Lift FR
  setLegRelativeAngles(1, 20, 15, -10);
  delay(100);

  // Phase 4: Place FR down
  setLegRelativeAngles(1, 0, 0, -10);
  delay(100);

  // Phase 5: Drag FL + FR right
  setLegRelativeAngles(0, 0, 0, 0);
  setLegRelativeAngles(1, 0, 0, 0);
  delay(100);

  // Phase 6: Lift RR
  setLegRelativeAngles(3, 20, -15, -10);
  delay(100);

  // Phase 7: Place RR down
  setLegRelativeAngles(3, 0, 0, 0);
  delay(100);

  // Phase 8: Lift RL
  setLegRelativeAngles(2, -20, 15, 10);
  delay(100);

  // Phase 9: Place RL down
  setLegRelativeAngles(2, 0, 0, 0);
  delay(100);
}

void moveForward(int steps) {
  standPosition();
  delay(100);
  for (int i = 0; i < steps; i++) {
    Serial.println("Moving forward.");
    stepForwardCycle();
  }
  standPosition();
  delay(100);
}

void moveBackward(int steps) {
  standPosition();
  delay(100);
  for (int i = 0; i < steps; i++) {
    Serial.println("Moving backward.");
    stepBackwardCycle();
  }
  standPosition();
  delay(100);
}

void moveLeft(int steps) {
  standPosition();
  delay(100);
  for (int i = 0; i < steps; i++) {
    Serial.println("Turning left.");
    turnLeftCycle();
  }
  standPosition();
  delay(100);
}

void moveRight(int steps) {
  standPosition();
  delay(100);
  for (int i = 0; i < steps; i++) {
    Serial.println("Turning right.");
    turnRightCycle();
  }
  standPosition();
  delay(100);
}

void setup() {
  Wire.begin();
  pwm.begin();
  pwm.setPWMFreq(50);

  delay(1000);
  powerUpPosition();  // the powering up sequence
  delay(2000);

  Serial.begin(115200);
  while (!Serial);
  Serial.println("Quadruped robot controller ready.");

  delay(2000);

  standPosition();
}

void loop() {
  // Accept commands via Serial Monitor for now
  if (Serial.available()) {
    String line = Serial.readStringUntil('\n');
    line.trim();
    if (line.length() == 0) return;

    if (line.startsWith("move,")) {
      int first = line.indexOf(',');
      int second = line.indexOf(',', first + 1);
      String dir  = line.substring(first + 1, second);
      int steps   = line.substring(second + 1).toInt();

      if (dir == "forward") moveForward(steps);
      else if (dir == "backward") moveBackward(steps);
      else if (dir == "left") moveLeft(steps);
      else if (dir == "right") moveRight(steps);
      else if (dir == "stand") standPosition();
      else if (dir == "flat") layFlatPosition();
      else if (dir == "sit") sitPosition();
      else if (dir == "paw") pawPosition();
      else if (dir == "greet") salutePosition();
      else standPosition();

      Serial.println("Finished instruction.");
    }

    // Testing direct servo control from Serial:
    else {
      int start = 0;
      while (start < line.length()) {
        int colon = line.indexOf(':', start);
        int space = line.indexOf(' ', start);
        if (space == -1) space = line.length();

        if (colon > start && colon < space) {
          int idx = line.substring(start, colon).toInt();
          int ang = line.substring(colon + 1, space).toInt();
          if (idx >= 0 && idx < NUM_SERVOS && ang >= 0 && ang <= 180) {
            pwm.setPWM(idx, 0, angleToPulse(ang));
            currentAngles[idx] = ang;
          }
        }
        start = space + 1;
      }
      Serial.println("Finished instruction.");
    }
    
  }
}

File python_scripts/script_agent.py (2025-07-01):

import os
import re
import json
import time
import requests
import subprocess
import serial
import time
import RPi.GPIO as GPIO

# For camera
from picamera2 import Picamera2

# Import the OpenAI Library
from openai import OpenAI

#############################################
# 1) SETUP & CONFIG
#############################################

# Adjustment values for the environment
WHISPER_BIN = "./whisper.cpp/build/bin/whisper-cli"     # Path to the whisper.cpp CLI
WHISPER_MODEL = "whisper.cpp/models/ggml-small.en.bin"  # whisper.cpp model file
AUDIO_FILE = "command.wav"                              # Audio file of the recording
IMAGE_FILE = "robot_view.jpg"                           # The picture taken from the camera

# Recording parameters
RECORD_SECONDS = 10
AUDIO_RATE = 44100
AUDIO_CHANNELS = 1
CHUNK = 1024

# TTS  parameters
volume = 1000   # Amplitude
speed = 175     # Speed
pitch = 40      # Pitch

# Arduino serial port configuration
ARDUINO_PORT = '/dev/arduino'   # /dev/arduino -> ttyACM0
ARDUINO_BAUDRATE = 115200

# Option to choose between the Whisper API or the local whisper.cpp CLI
USE_API_WHISPER = True

# OpenAI/GPT initialization
client = OpenAI(
    api_key="your_key"  # Replace with your actual API key
)

assistant_id="assistant_id"    # The assistant ID to use
thread_id="thread_script"                       # The thread ID

# Pin setup for the ultrasonic sensor
TRIG_LEFT = 23
ECHO_LEFT = 24
TRIG_RIGHT = 27
ECHO_RIGHT = 22

#############################################
# 2) FUNCTION TO RECORD AUDIO
#############################################
def record_audio(duration=RECORD_SECONDS, output_file=AUDIO_FILE, rate=AUDIO_RATE, channels=AUDIO_CHANNELS, chunk=CHUNK):
    """
    Record audio by calling an external Python script with sudo privileges.
    """
    print(f"[System] Calling audio recording script with sudo...")
    
    # Command to call the external script with sudo
    subprocess.run(['sudo', 'python3', 'record_audio.py', output_file, str(duration), str(rate), str(channels), str(chunk)], check=True)

#############################################
# 3) FUNCTION TO RUN WHISPER TRANSCRIPTION
#############################################
def transcribe_with_whisper(wav_file=AUDIO_FILE):
    """
    Use the whisper.cpp CLI tool to transcribe the given wav file.
    Returns the transcribed text (str).
    If Whisper produces no text, return an empty string.
    """
    if not USE_API_WHISPER:
        # Use the local Whisper to transcribe the audio
        if not os.path.exists(wav_file):
            print(f"[Whisper] WAV file not found: {wav_file}")
            return ""

        if not os.path.exists(WHISPER_BIN):
            print(f"[Whisper] Whisper CLI not found at: {WHISPER_BIN}")
            return ""

        cmd = [
            WHISPER_BIN,
            "-m", WHISPER_MODEL,
            "-f", wav_file,
            # optional flags if needed, e.g. language, etc.
        ]

        print("[Whisper] Running whisper.cpp CLI to transcribe audio...")
        try:
            result = subprocess.run(cmd, capture_output=True, text=True)
            if result.returncode != 0:
                print(f"[Whisper] Error during transcription: {result.stderr}")
                return ""
            # The transcript is often at the end of stdout, but this can vary by version
            output_lines = result.stdout.strip().split("\n")
            if len(output_lines) == 0:
                return ""
            # Usually the final line is the recognized text
            transcript = output_lines[-1].strip()
            print(f"[Whisper] Transcription: {transcript}")
            return transcript
        except Exception as e:
            print(f"[Whisper] Exception running whisper CLI: {e}")
            return ""
    else:
        transcript = ""
        # Use the API to transcribe the audio
        print("[Whisper] Transcribing audio with API...")
        try:
            # Open the audio file
            audio_file = open(wav_file, "rb")
        except FileNotFoundError:
            print(f"[Whisper] WAV file not found: {wav_file}")
        try:
            # Call the API to transcribe the audio
            transcript = client.audio.transcriptions.create(
                model="whisper-1",
                file=audio_file
            )
        except Exception as e:
            print(f"[Whisper] Error during transcription: {e}")

        return transcript.text

#############################################
# 4) FUNCTION TO CAPTURE AN IMAGE
#############################################
def capture_image(output_file=IMAGE_FILE):
    """
    Capture an image from the Pi camera using libcamera and save to `output_file`.
    """
    # Run the libcamera-jpeg command
    print("[Camera] Running the libcamera command...")
    subprocess.run(["libcamera-jpeg", "-o", output_file, "--timeout", "0.1"])

    print(f"[Camera] Image saved as {output_file}")
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

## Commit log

2025-06-24 Added the project 3D models
    [Bearing_adapter.stl, Camera_mount.stl, Electronics_mount.stl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]
2025-07-01 Added Arduino files
